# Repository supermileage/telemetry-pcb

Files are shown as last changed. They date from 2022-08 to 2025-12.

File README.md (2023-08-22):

# Telemetry PCB

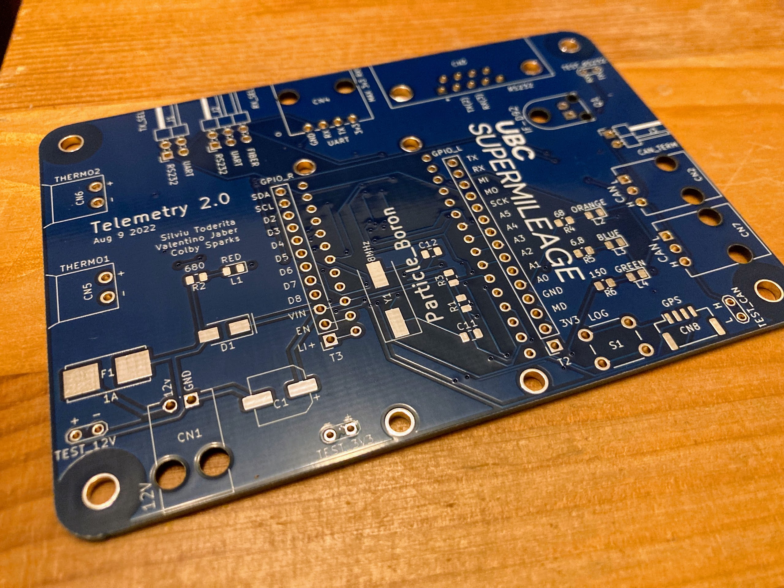
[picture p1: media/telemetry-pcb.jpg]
Telemetry 2.0 Circuit Board


Printed Circuit Board design for the Supermileage Telemetry Module. More information on its functionality can be found in the [firmware repo](https://github.com/supermileage/telemetry-firmware/tree/master).

The PCB is a 2-layer design, intended to be manufactured with 1oz copper. It was designed to be as small and as versatile as possible, to fit into tight spaces on multiple vehicles. The PCB features:

- Particle Boron Microcontroller with built-in LTE Connection
- LMS6DSO Accelerometer & Gyroscope
- 2x MAX31855K Thermocouple ICs with 2 Thermocouple inputs
- MCP2515 CAN Controller, TCAN332 CAN Transciever, 2x CAN ports
- Switchable TTL UART, RS232 UART (MAX3232), or optical UART (IF-D92)
- Connector for external i2c GPS module
- LEDs and button for monitoring & control

## Schematic Preview

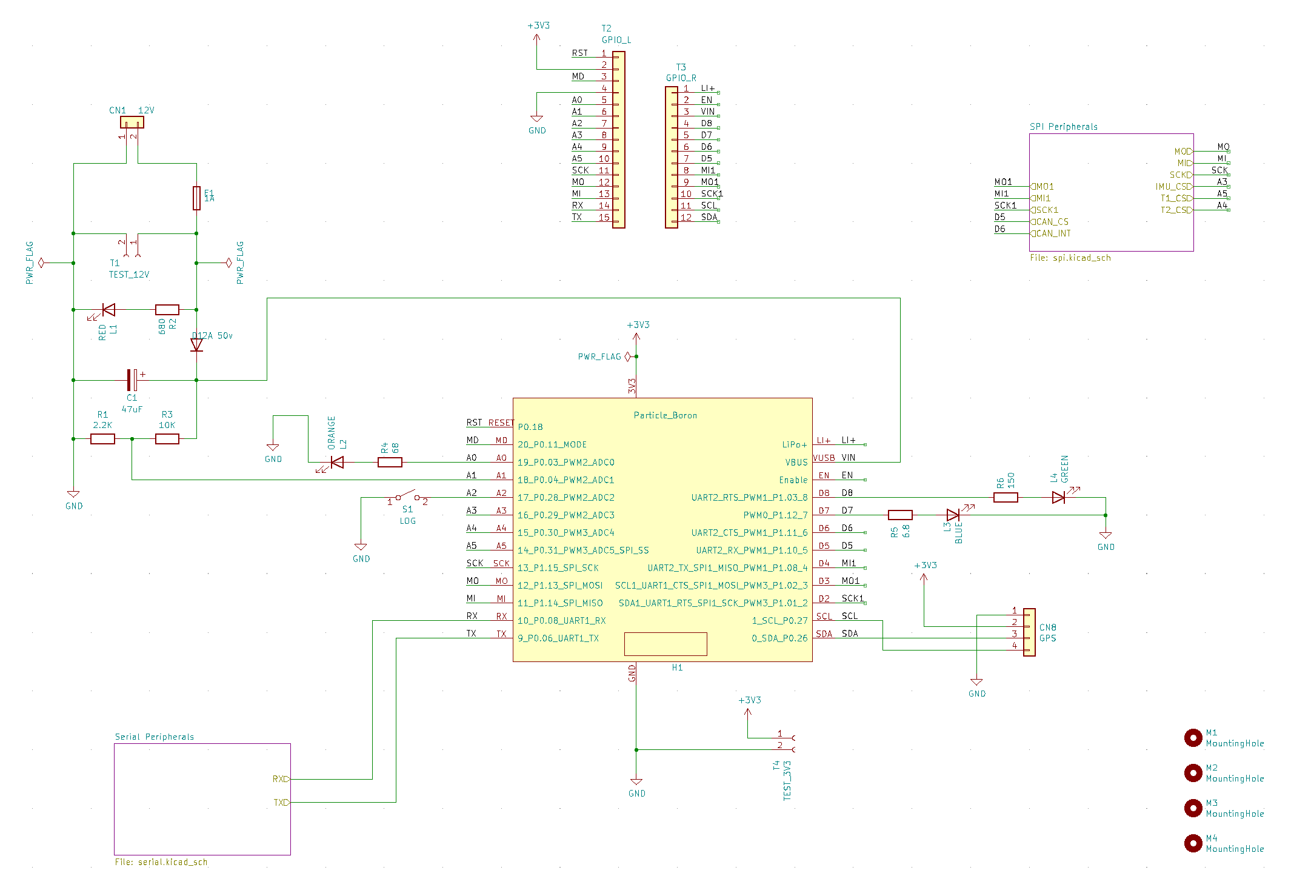
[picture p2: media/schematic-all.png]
Schematic All


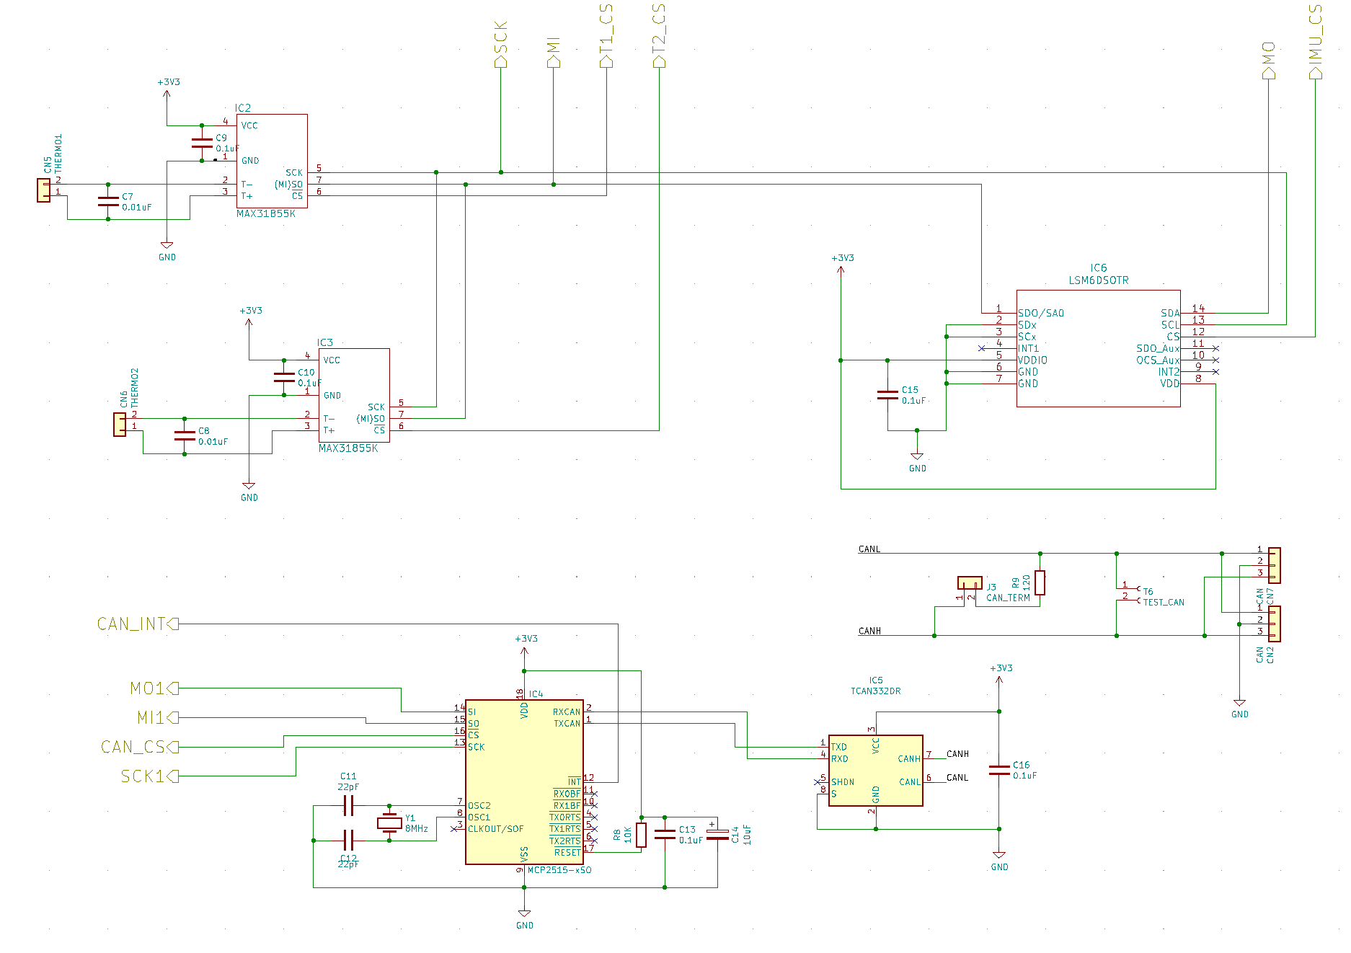
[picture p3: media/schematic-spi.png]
Schematic SPI


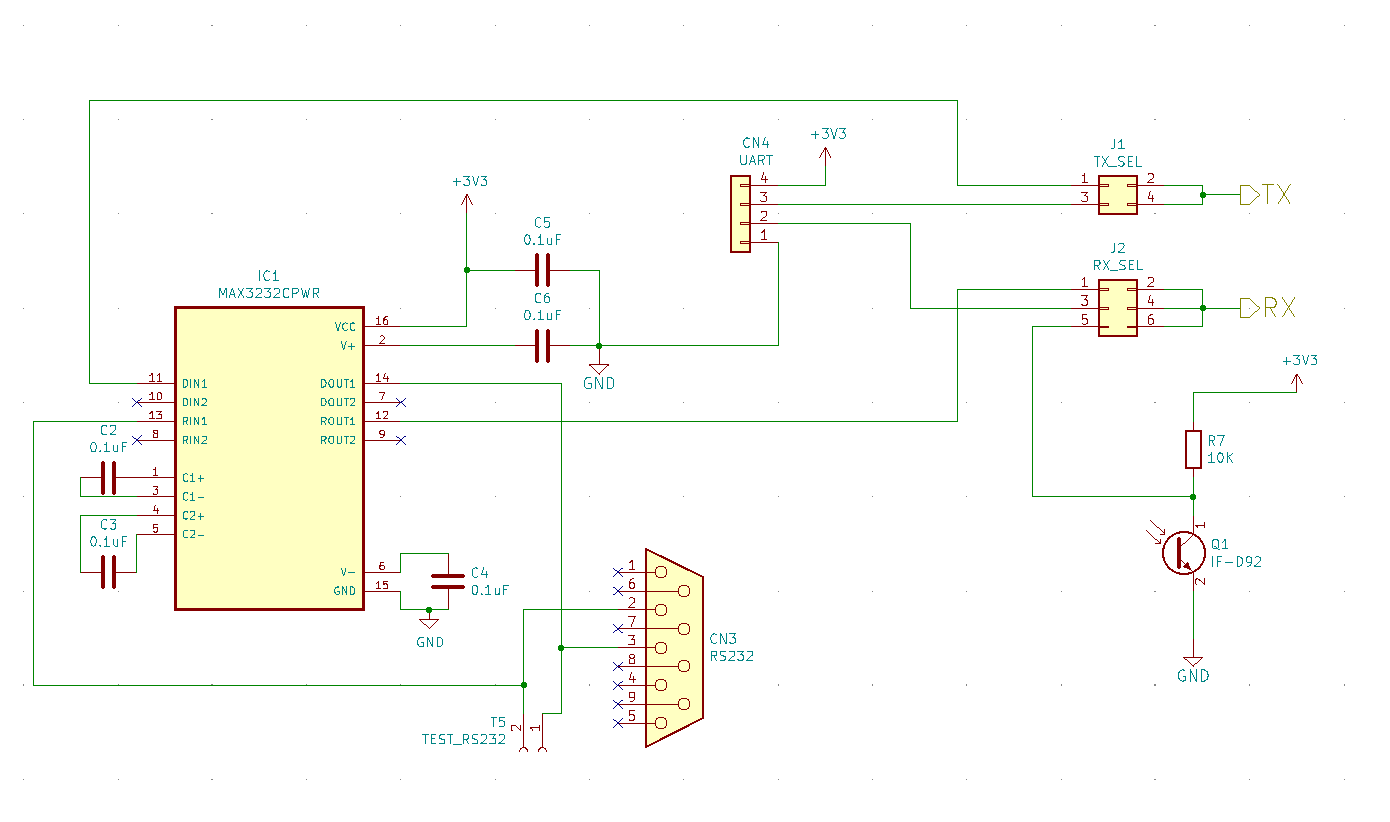
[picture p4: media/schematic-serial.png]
Schematic Serial


## PCB Preview

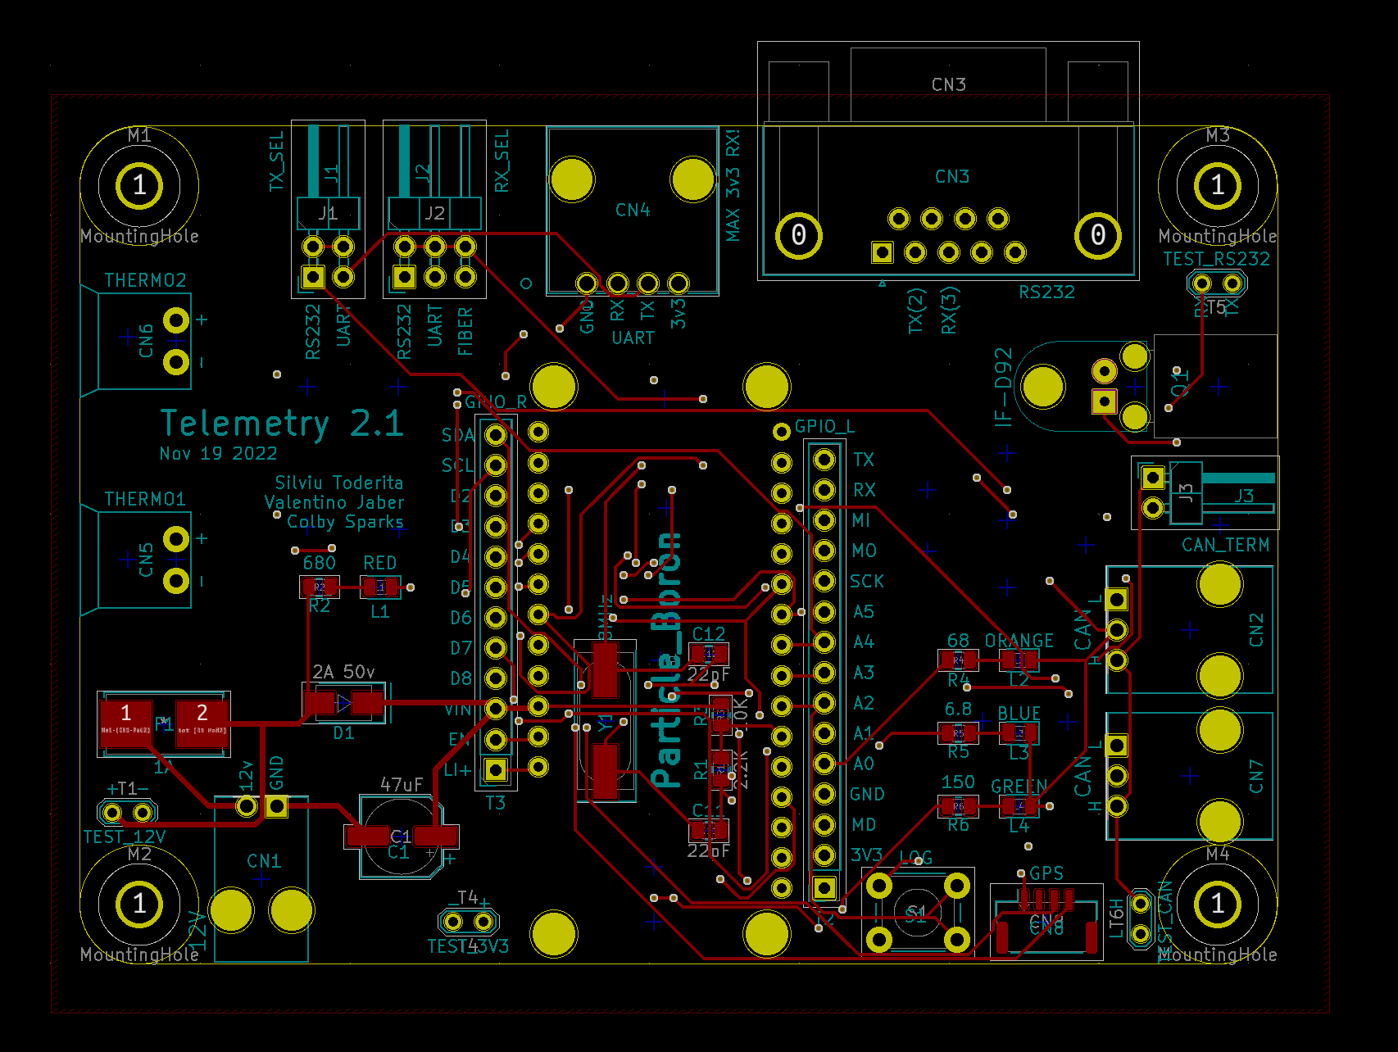
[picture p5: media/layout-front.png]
Layout Front


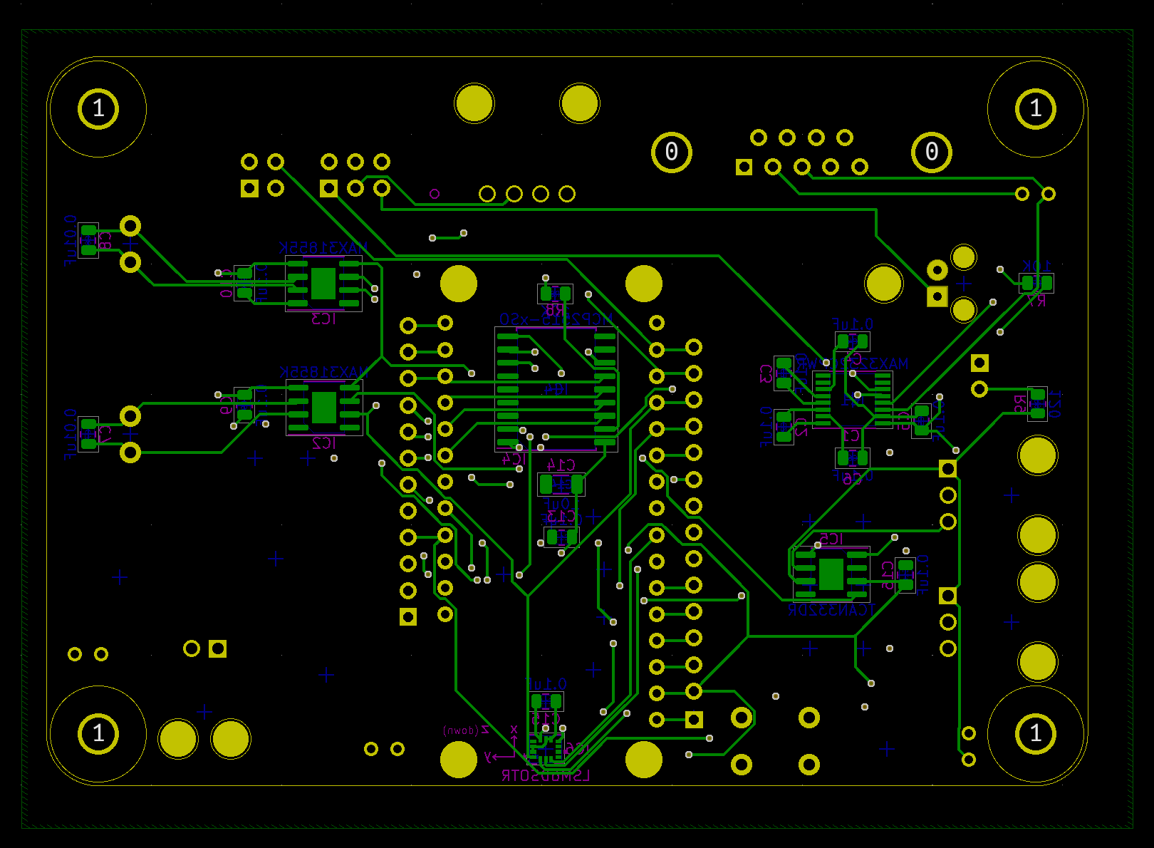
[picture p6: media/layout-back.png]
Layout Back


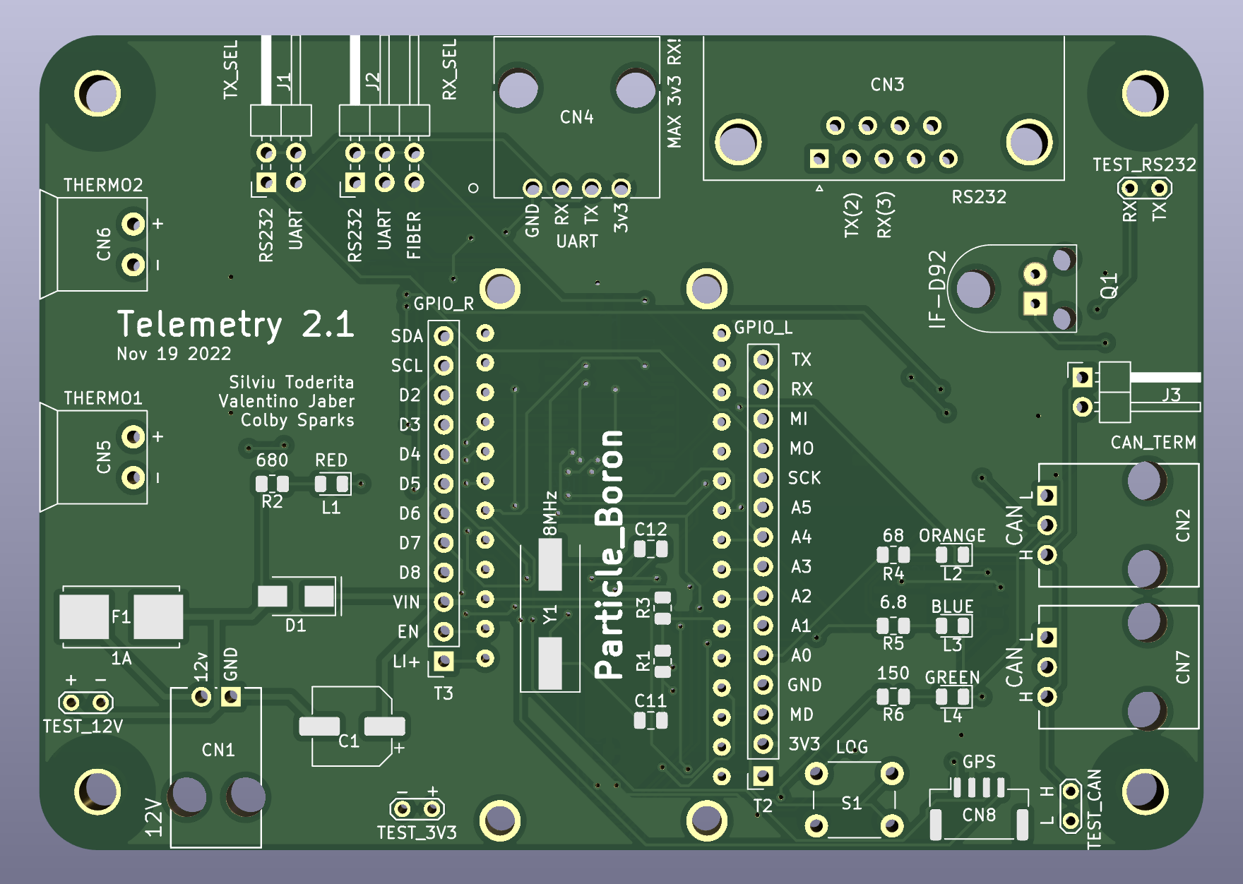
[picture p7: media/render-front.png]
Render Front


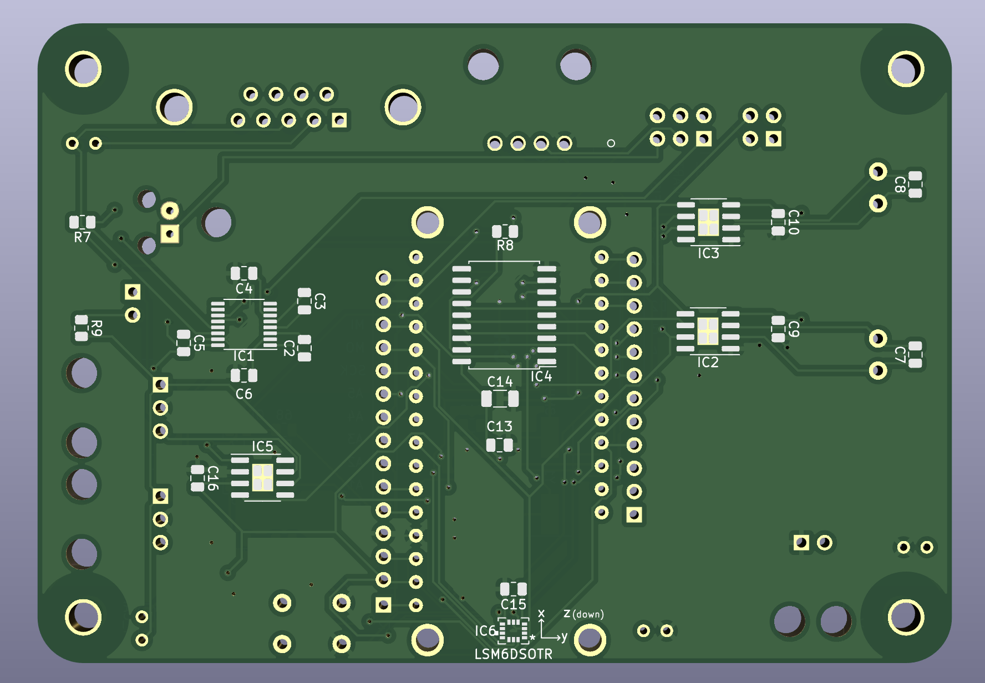
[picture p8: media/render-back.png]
Render Back


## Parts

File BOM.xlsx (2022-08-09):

*Designator | *Qty | Manufacturer | *Mfg Part # | Description / Value | *Package/Footprint | Type | DigiKey URL | Source
C1 | 1 | Wurth Elektronik | 865080543009 | CAP ALUM 47UF 20% 35V SMD | Radial 6.3mm | SMD | https://www.digikey.ca/en/products/detail/w%C3%BCrth-elektronik/865080543009/5728103 | Digikey
C2,C3,C4,C5,C6,C9,C10,C13,C15,C16 | 10 | Samsung Electro-Mechanics | CL21B104KBCNNNC | CAP CER 0.1UF 50V X7R 0805 | 0805 | SMD | https://www.digikey.ca/en/products/detail/samsung-electro-mechanics/CL21B104KBCNNNC/3886661 | Digikey
C7,C8 | 2 | Kemet | C0805C103K1RAC7800 | CAP CER 10000PF 100V X7R 0805 | 0805 | SMD | https://www.digikey.ca/en/products/detail/kemet/C0805C103K1RAC7800/411158 | Digikey
C11,C12 | 2 | Kemet | C0805C220J5GAC7800 | CAP CER 22PF 50V C0G/NP0 0805 | 0805 | SMD | https://www.digikey.ca/en/products/detail/kemet/C0805C220J5GAC7800/411112 | Digikey
C14 | 1 | KYOCERA AVX | TAJA106K016RNJ | CAP TANT 10UF 10% 16V 1206 | 1206 | SMD | https://www.digikey.ca/en/products/detail/kyocera-avx/TAJA106K016RNJ/563762 | Digikey
CN1 | 1 | Molex | 705510001 | CONN HEADER R/A 2POS 2.54MM | 1x4POS | Through-Hole | https://www.digikey.ca/en/products/detail/molex/0705510001/2421652 | Digikey
CN2,CN7 | 2 | Molex | 705510002 | CONN HEADER R/A 3POS 2.54MM | 1x3POS | Through-Hole | https://www.digikey.ca/en/products/detail/molex/0705510002/3468756?s=N4IgTCBcDaIOwAYCsSCMCMQLoF8g | Digikey
CN3 | 1 | Amphenol ICC (FCI) | LD09P13A4GX00LF | CONN D-SUB PLUG 9POS R/A SLDR | D-SUB 9POS | Through-Hole | https://www.digikey.ca/en/products/detail/amphenol-icc-fci/LD09P13A4GX00LF/4997285 | Digikey
CN4 | 1 | Molex | 0705510003 | CONN HEADER R/A 4POS 2.54MM | 1x5POS | Through-Hole | https://www.digikey.ca/en/products/detail/molex/0705510003/3468757 | Digikey
CN5,CN6 | 2 | TE Connectivity AMP Connectors | 284512-2 | TERM BLOCK HDR 2POS 90DEG 3.5MM | 1x2POS | Through-Hole | https://www.digikey.ca/en/products/detail/te-connectivity/284512-2/1150185 | Digikey
CN8 | 1 | JST Sales America Inc. | S4B-ZR-SM4A-TF(LF)(SN) | CONN HEADER SMD R/A 4POS 1.5MM | 1x4POS | SMD | https://www.digikey.ca/en/products/detail/jst-sales-america-inc/S4B-ZR-SM4A-TF-LF-SN/926602 | Digikey
D1 | 1 | Diodes Incorporated | S1A-13-F | DIODE GEN PURP 50V 1A SMA | SMA | SMD | https://www.digikey.ca/en/products/detail/diodes-incorporated/S1A-13-F/749977 | Digikey
F1 | 1 | Littelfuse Inc. | 0154001.DRL | FUSE BRD MNT 1A 125VAC/VDC 2SMD | 2-SMD | SMD | https://www.digikey.ca/en/products/detail/littelfuse-inc/0154001-DRL/2520371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 | Digikey
H1 (A) | 1 | Sullins Connector Solutions | S7014-ND | CONN HDR 16POS 0.1 TIN PCB | 1x16POS | Through-Hole | https://www.digikey.ca/en/products/detail/sullins-connector-solutions/PPTC161LFBN-RC/810154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 | Digikey
H1 (B) | 1 | Sullins Connector Solutions | S6100-ND | CONN HDR 12POS 0.1 TIN PCB | 1x12POS | Through-Hole | https://www.digikey.ca/en/products/detail/sullins-connector-solutions/PPTC121LFBN-RC/807231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 | Digikey
IC1 | 1 | Analog Devices Inc./Maxim Integrated | MAX3232ECUE+T | IC TRANSCEIVER FULL 2/2 16TSSOP | 16-TSSOP | SMD | https://www.digikey.ca/en/products/detail/analog-devices-inc-maxim-integrated/MAX3232ECUE-T/1515210 | Digikey
IC2,IC3 | 2 | Maxim Integrated | MAX31855KASA+T | IC CONV THERMOCOUPLE-DGTL SOIC | 8-SOIC | SMD | https://www.digikey.ca/en/products/detail/analog-devices-inc-maxim-integrated/MAX31855KASA/2591564 | Digikey
IC4 | 1 | Microchip Technology | MCP2515T-I/SOCT-ND | IC CAN CONTROLLER W/SPI 18SOIC | 18-SOIC | SMD | https://www.digikey.ca/en/products/detail/microchip-technology/MCP2515T-I-SO/593681 | ???
IC5 | 1 | Analog Devices Inc./Maxim Integrated | MAX33041EASA+ | IC CAN TXRX 3.3V 2MBPS SOIC | 8-SOIC | SMD | https://www.digikey.ca/en/products/detail/analog-devices-inc-maxim-integrated/MAX33041EASA/15286828 | Digikey
IC6 | 1 | STMicroelectronics | LSM6DSOTR | CONSUMER MEMS | 14-LGA | SMD | https://www.digikey.ca/en/products/detail/stmicroelectronics/LSM6DSOTR/9586579 | Digikey
J1 | 1 | Amphenol ICC (FCI) | 10129382-906003BLF | CONN HEADER R/A 6POS 2.54MM | 2x3POS | Through-Hole | https://www.digikey.ca/en/products/detail/amphenol-icc-fci/10129382-906003BLF/7916129 | Digikey
J2 | 1 | Sullins Connector Solutions | PRPC002DBAN-M71RC | CONN HEADER R/A 4POS 2.54MM | 2x2POS | Through-Hole | https://www.digikey.ca/en/products/detail/sullins-connector-solutions/PRPC002DBAN-M71RC/2775721 | Digikey
J3 | 1 | Amphenol ICC (FCI) | 10129379-902001BLF | CONN HEADER R/A 2POS 2.54MM | 1x2POS | Through-Hole | https://www.digikey.ca/en/products/detail/amphenol-icc-fci/10129379-902001BLF/7915977 | Digikey
L1 | 1 | Lite-On Inc. | LTST-C170KRKT | LED RED CLEAR SMD (680) | 0805 | SMD | https://www.digikey.ca/en/products/detail/lite-on-inc/LTST-C170KRKT/386779 | Digikey
L2 | 1 | Lite-On Inc. | LTST-C170KFKT | LED ORANGE CLEAR SMD (68) | 0805 | SMD | https://www.digikey.ca/en/products/detail/lite-on-inc/LTST-C170KFKT/386775 | Digikey
L3 | 1 | Lite-On Inc. | LTST-C170TBKT | LED BLUE CLEAR SMD (6.8) | 0805 | SMD | https://www.digikey.ca/en/products/detail/lite-on-inc/LTST-C170TBKT/388527 | Digikey
L4 | 1 | Lite-On Inc. | LTST-C170GKT | LED GREEN CLEAR SMD (150) | 0805 | SMD | https://www.digikey.ca/en/products/detail/lite-on-inc/LTST-C170GKT/269226 | Digikey
Q1 | 1 | Industrial Fiber Optics | IF-D92 | PHOTOTRANSISTOR FIBER OPTIC |  | Through-Hole | https://www.digikey.ca/en/products/detail/industrial-fiber-optics/IF-D92/243778?s=N4IgTCBcDaIJYDMC0ATAnBAugXyA | Digikey
R1 | 1 | Stackpole Electronics Inc | RMCF0805FT2K20 | RES 2.2K OHM 1% 1/8W 0805 | 0805 | SMD | https://www.digikey.ca/en/products/detail/stackpole-electronics-inc/RMCF0805FT2K20/1760345 | Digikey
R2 | 1 | Stackpole Electronics Inc | RMCF0805FT680R | RES 680 OHM 1% 1/8W 0805 | 0805 | SMD | https://www.digikey.ca/en/products/detail/stackpole-electronics-inc/RMCF0805FT680R/1760531 | Digikey
R3,R7,R8 | 3 | Stackpole Electronics Inc | RMCF0805JT10K0 | RES 10K OHM 5% 1/8W 0805 | 0805 | SMD | https://www.digikey.ca/en/products/detail/stackpole-electronics-inc/RMCF0805JT10K0/1757762 | Digikey
R4 | 1 | Stackpole Electronics Inc | RMCF0805FT68R0 | RES 68 OHM 1% 1/8W 0805 | 0805 | SMD | https://www.digikey.ca/en/products/detail/stackpole-electronics-inc/RMCF0805FT68R0/1713312 | Digikey
R5 | 1 | YAGEO | RC0805FR-076R8L | RES 6.8 OHM 1% 1/8W 0805 | 0805 | SMD | https://www.digikey.ca/en/products/detail/yageo/RC0805FR-076R8L/728065 | Digikey
R6 | 1 | Stackpole Electronics Inc | RMCF0805JT150R | RES 150 OHM 5% 1/8W 0805 | 0805 | SMD | https://www.digikey.ca/en/products/detail/stackpole-electronics-inc/RMCF0805JT150R/1757820 | Digikey
R9 | 1 | Stackpole Electronics Inc | RMCF0805JT120R | RES 120 OHM 5% 1/8W 0805 | 0805 | SMD | https://www.digikey.ca/en/products/detail/stackpole-electronics-inc/RMCF0805JT120R/1757777 | Digikey
S1 | 1 | TE Connectivity ALCOSWITCH Switches | 3-1825910-1 | SWITCH TACTILE SPST-NO 0.05A 24V | 6mm | Through-Hole | https://www.digikey.ca/en/products/detail/te-connectivity-alcoswitch-switches/3-1825910-1/1632529 | Digikey
Y1 | 1 | Abracon LLC | ABLS2-8.000MHZ-D4Y-T | 8 MHz ±30ppm Crystal 18pF 80 Ohms HC-49/US | HC-49/US | SMD | https://www.digikey.ca/en/products/detail/abracon-llc/ABLS2-8-000MHZ-D4Y-T/2001231 | Digikey
Not on PCB:
Microcontroller | 1 | Particle Industries, Inc. | BRN402 | BORON LTE |  | Through-Hole | https://www.digikey.ca/en/products/detail/particle-industries-inc/BRN402/9681356 | ???
GPS | 1 | SparkFun Electronics | GPS-15210 | SPARKFUN GPS BREAKOUT - CHIP ANT |  |  | https://www.digikey.ca/en/products/detail/sparkfun-electronics/GPS-15210/10064422 | Digikey
Mounting Screws | 4 |  |  | M3x6 Screw |  |  |  | Lee's Electronics
Jumpers | 3 | Sullins Connector Solutions | QPC02SXGN-RC | CONN JUMPER SHORTING .100" GOLD | 1x2POS |  | https://www.digikey.ca/en/products/detail/sullins-connector-solutions/QPC02SXGN-RC/2618262 | Digikey
Connector Power | 1 | Molex | 0050579702 | CONN FEMALE HSG POS LTCH 2CKT | 1x2POS |  | https://www.digikey.ca/en/products/detail/molex/0050579702/2421209 | Digikey
Connector CAN | 2 | Molex | 50579703 | CONN HSG 3POS .100 SINGLE VER N | 1x3POS |  | https://www.digikey.ca/en/products/detail/molex/0050579703/2731437 | Digikey
Connector UART | 1 | Molex | 0050579704 | CONN HSG 4POS .100 SINGLE VER N | 1x4POS |  | https://www.digikey.ca/en/products/detail/molex/0050579704/2731443 | Digikey
Connector Thermocouple | 2 | TE Connectivity AMP Connectors | 284506-2 | TERM BLOCK PLUG 2POS STR 3.5MM | 1x2POS |  | https://www.digikey.ca/en/products/detail/te-connectivity-amp-connectors/284506-2/1827035 | Digikey
Molex Pins | 12 | Molex | 16020086 | CONN SOCKET 22-24AWG CRIMP TIN |  |  | https://www.digikey.ca/en/products/detail/molex/0016020086/467788 | Digikey
Connector GPS | 1 | JST Sales America Inc. | ZHR-4 | CONN RCPT HSG 4POS 1.50MM | 1x4POS |  | https://www.digikey.ca/en/products/detail/jst-sales-america-inc/ZHR-4/608643 | ???
GPS Pre-Crimped Pins | 1 | JST Sales America Inc. | ASZHSZH28K51 | JUMPER SZH-002T-P0.5 X2 2" |  |  | https://www.digikey.ca/en/products/detail/jst-sales-america-inc/ASZHSZH28K51/6009454 | Digikey
Spare Fuse |  | Bel Fuse Inc. | 0679L1000-05 | FUSE BRD MNT 1A 125VAC/VDC | 2-SMD |  | https://www.digikey.ca/en/products/detail/bel-fuse-inc/0679L1000-05/5844030 | Digikey
ECU Cable |  |  |  | RS232 Cable (Straight-Through) |  |  |  | Amazon
FC Fiber |  |  |  | 2.2mm Fiber Optic Wire
Thermocouples |  |  |  | 1M insulated K-Type Thermocouple
Case |  |  |  | 3D Printed Custom Case
USB Cable |  |  |  | Micro-USB Cable
 |  |  |  |  |  | u

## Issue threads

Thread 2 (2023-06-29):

Fix button footprint

cosparks, 2023-06-29:
Orientaion of connectors is wrong.  Swap 3.3V and ground

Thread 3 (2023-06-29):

Add through-hole connector with latch for GPS

cosparks, 2023-06-29:
The surface mount connector for GPS has been problematic.  There is no latch so it can be pulled out very easily, and twice we have stripped the pads by pushing too hard against it.  We ran into both of these issues during competition.

See if a molex micro or nanofit connector would fit on the board.

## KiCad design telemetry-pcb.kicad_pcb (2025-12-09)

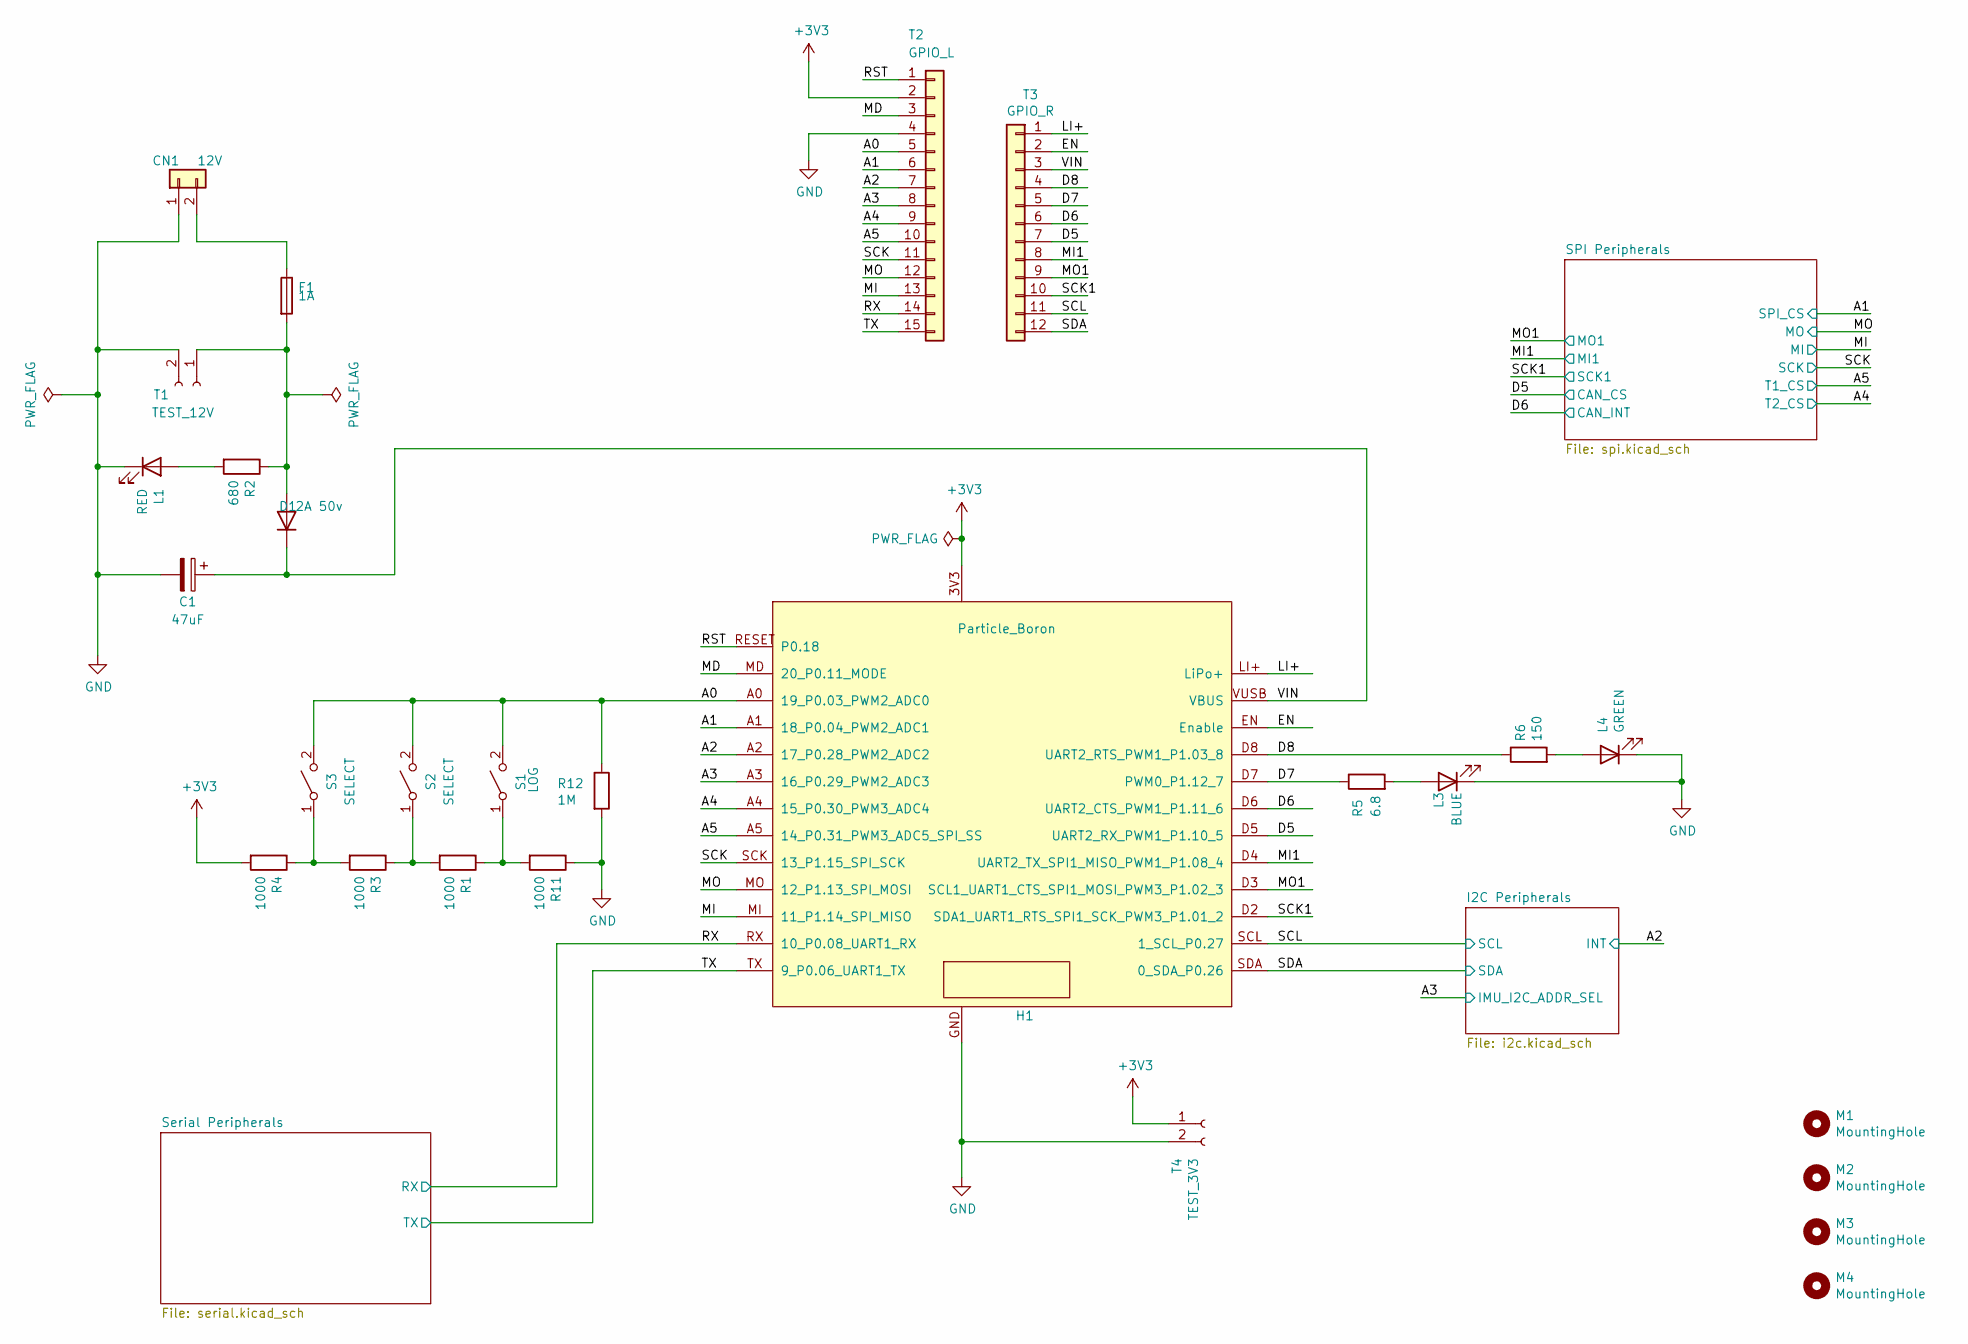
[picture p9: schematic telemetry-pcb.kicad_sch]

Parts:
C1: 47uF; CP_Elec_6.3x5.4
CN1: 12V; molex_sl_1x02_horizontal
D1: 2A 50v; D_SMA
F1: 1A; 0154001.DRL
H1: Particle_Boron; Particle_boron
L1: RED; LED_0805_2012Metric
L3: BLUE; LED_0805_2012Metric
L4: GREEN; LED_0805_2012Metric
M1, M2, M3, M4: MountingHole; MountingHole_3.2mm_M3
R1, R3, R4, R11: 1000; R_0805_2012Metric
R2: 680; R_0805_2012Metric
R5: 6.8; R_0805_2012Metric
R6: 150; R_0805_2012Metric
R12: 1M; R_0805_2012Metric
S1: LOG; SW_PUSH_6mm_H13mm
S2, S3: SELECT; SW_PUSH_6mm_H13mm
T1: TEST_12V; TestPoint_2Pads_Pitch2.54mm_Drill0.8mm
T2: GPIO_L; Boron_Pins_L
T3: GPIO_R; Boron_Pins_R
T4: TEST_3V3; TestPoint_2Pads_Pitch2.54mm_Drill0.8mm

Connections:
+3V3: H1.3V3, R4.2, T2.2, T4.1; also elsewhere on the board
/A0: H1.A0 (19_P0.03_PWM2_ADC0), R12.1, S1.2 (B), S2.2 (B), S3.2 (B), T2.5
/A1: H1.A1 (18_P0.04_PWM2_ADC1), T2.6; also elsewhere on the board
/A2: H1.A2 (17_P0.28_PWM2_ADC2), T2.7; also elsewhere on the board
/A3: H1.A3 (16_P0.29_PWM2_ADC3), T2.8; also elsewhere on the board
/A4: H1.A4 (15_P0.30_PWM3_ADC4), T2.9; also elsewhere on the board
/A5: H1.A5 (14_P0.31_PWM3_ADC5_SPI_SS), T2.10; also elsewhere on the board
/D5: H1.D5 (UART2_RX_PWM1_P1.10_5), T3.7; also elsewhere on the board
/D6: H1.D6 (UART2_CTS_PWM1_P1.11_6), T3.6; also elsewhere on the board
/D7: H1.D7 (PWM0_P1.12_7), R5.1, T3.5
/D8: H1.D8 (UART2_RTS_PWM1_P1.03_8), R6.1, T3.4
/EN: H1.EN (Enable), T3.2
/LI+: H1.LI+ (LiPo+), T3.1
/MD: H1.MD (20_P0.11_MODE), T2.3
/MI: H1.MI (11_P1.14_SPI_MISO), T2.13; also elsewhere on the board
/MI1: H1.D4 (UART2_TX_SPI1_MISO_PWM1_P1.08_4), T3.8; also elsewhere on the board
/MO: H1.MO (12_P1.13_SPI_MOSI), T2.12; also elsewhere on the board
/MO1: H1.D3 (SCL1_UART1_CTS_SPI1_MOSI_PWM3_P1.02_3), T3.9; also elsewhere on the board
/RST: H1.RESET (P0.18), T2.1
/RX: H1.RX (10_P0.08_UART1_RX), T2.14; also elsewhere on the board
/SCK: H1.SCK (13_P1.15_SPI_SCK), T2.11; also elsewhere on the board
/SCK1: H1.D2 (SDA1_UART1_RTS_SPI1_SCK_PWM3_P1.01_2), T3.10; also elsewhere on the board
/SCL: H1.SCL (1_SCL_P0.27), T3.11; also elsewhere on the board
/SDA: H1.SDA (0_SDA_P0.26), T3.12; also elsewhere on the board
/TX: H1.TX (9_P0.06_UART1_TX), T2.15; also elsewhere on the board
/VIN: C1.1, D1.1 (K), H1.VUSB (VBUS), T3.3
GND: C1.2, CN1.1, H1.GND, L1.1 (K), L3.1 (K), L4.1 (K), R11.1, R12.2, T1.2, T2.4, T4.2; also elsewhere on the board
unnamed: CN1.2, F1.1
unnamed: D1.2 (A), F1.2, R2.1, T1.1
unnamed: L1.2 (A), R2.2
unnamed: L3.2 (A), R5.2
unnamed: L4.2 (A), R6.2
unnamed: R1.1, R11.2, S1.1 (A)
unnamed: R1.2, R3.1, S2.1 (A)
unnamed: R3.2, R4.1, S3.1 (A)

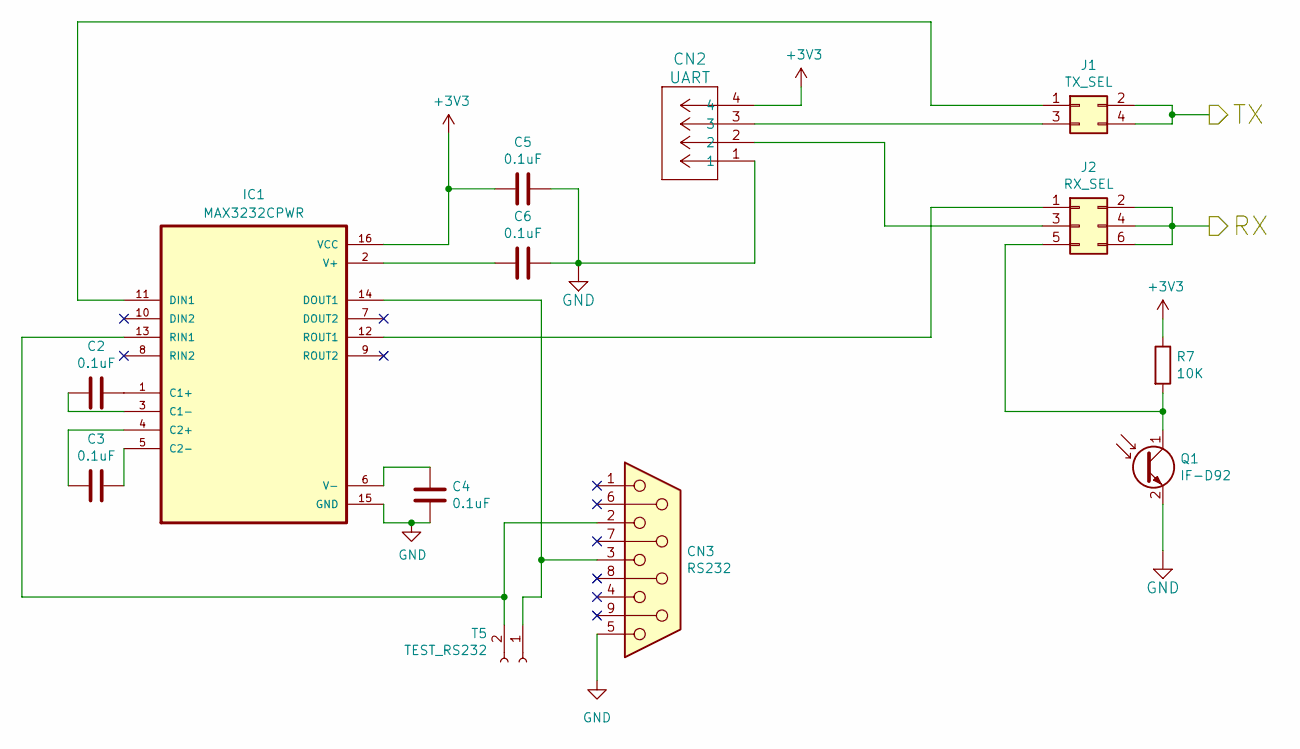
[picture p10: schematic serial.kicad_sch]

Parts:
C2, C3, C4, C5, C6: 0.1uF; C_0805_2012Metric
CN2: UART; CONN_SD-43650-001_04_MOL
CN3: RS232; DSUB-9_Female_Horizontal_P2.77x2.84mm_EdgePinOffset7.70mm_H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
IC1: MAX3232CPWR; TSSOP-16_4.4x5mm_P0.65mm
J1: TX_SEL; PinHeader_2x02_P2.54mm_Horizontal
J2: RX_SEL; PinHeader_2x03_P2.54mm_Horizontal
Q1: IF-D92
R7: 10K; R_0805_2012Metric
T5: TEST_RS232; TestPoint_2Pads_Pitch2.54mm_Drill0.8mm

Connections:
+3V3: C5.2, CN2.4, IC1.16 (VCC), R7.1; also elsewhere on the board
/RX: J2.2, J2.4, J2.6; also elsewhere on the board
/TX: J1.2, J1.4; also elsewhere on the board
GND: C4.2, C5.1, C6.1, CN2.1, CN3.5, IC1.15 (GND), Q1.2 (E); also elsewhere on the board
unnamed: C2.1, IC1.1 (C1+)
unnamed: C2.2, IC1.3 (C1-)
unnamed: C3.2, IC1.4 (C2+)
unnamed: C3.1, IC1.5 (C2-)
unnamed: IC1.11 (DIN1), J1.1
unnamed: CN3.3, IC1.14 (DOUT1), T5.1
unnamed: CN3.2, IC1.13 (RIN1), T5.2
unnamed: IC1.12 (ROUT1), J2.1
unnamed: C6.2, IC1.2 (V+)
unnamed: C4.1, IC1.6 (V-)
unnamed: CN2.3, J1.3
unnamed: CN2.2, J2.3
unnamed: J2.5, Q1.1 (C), R7.2

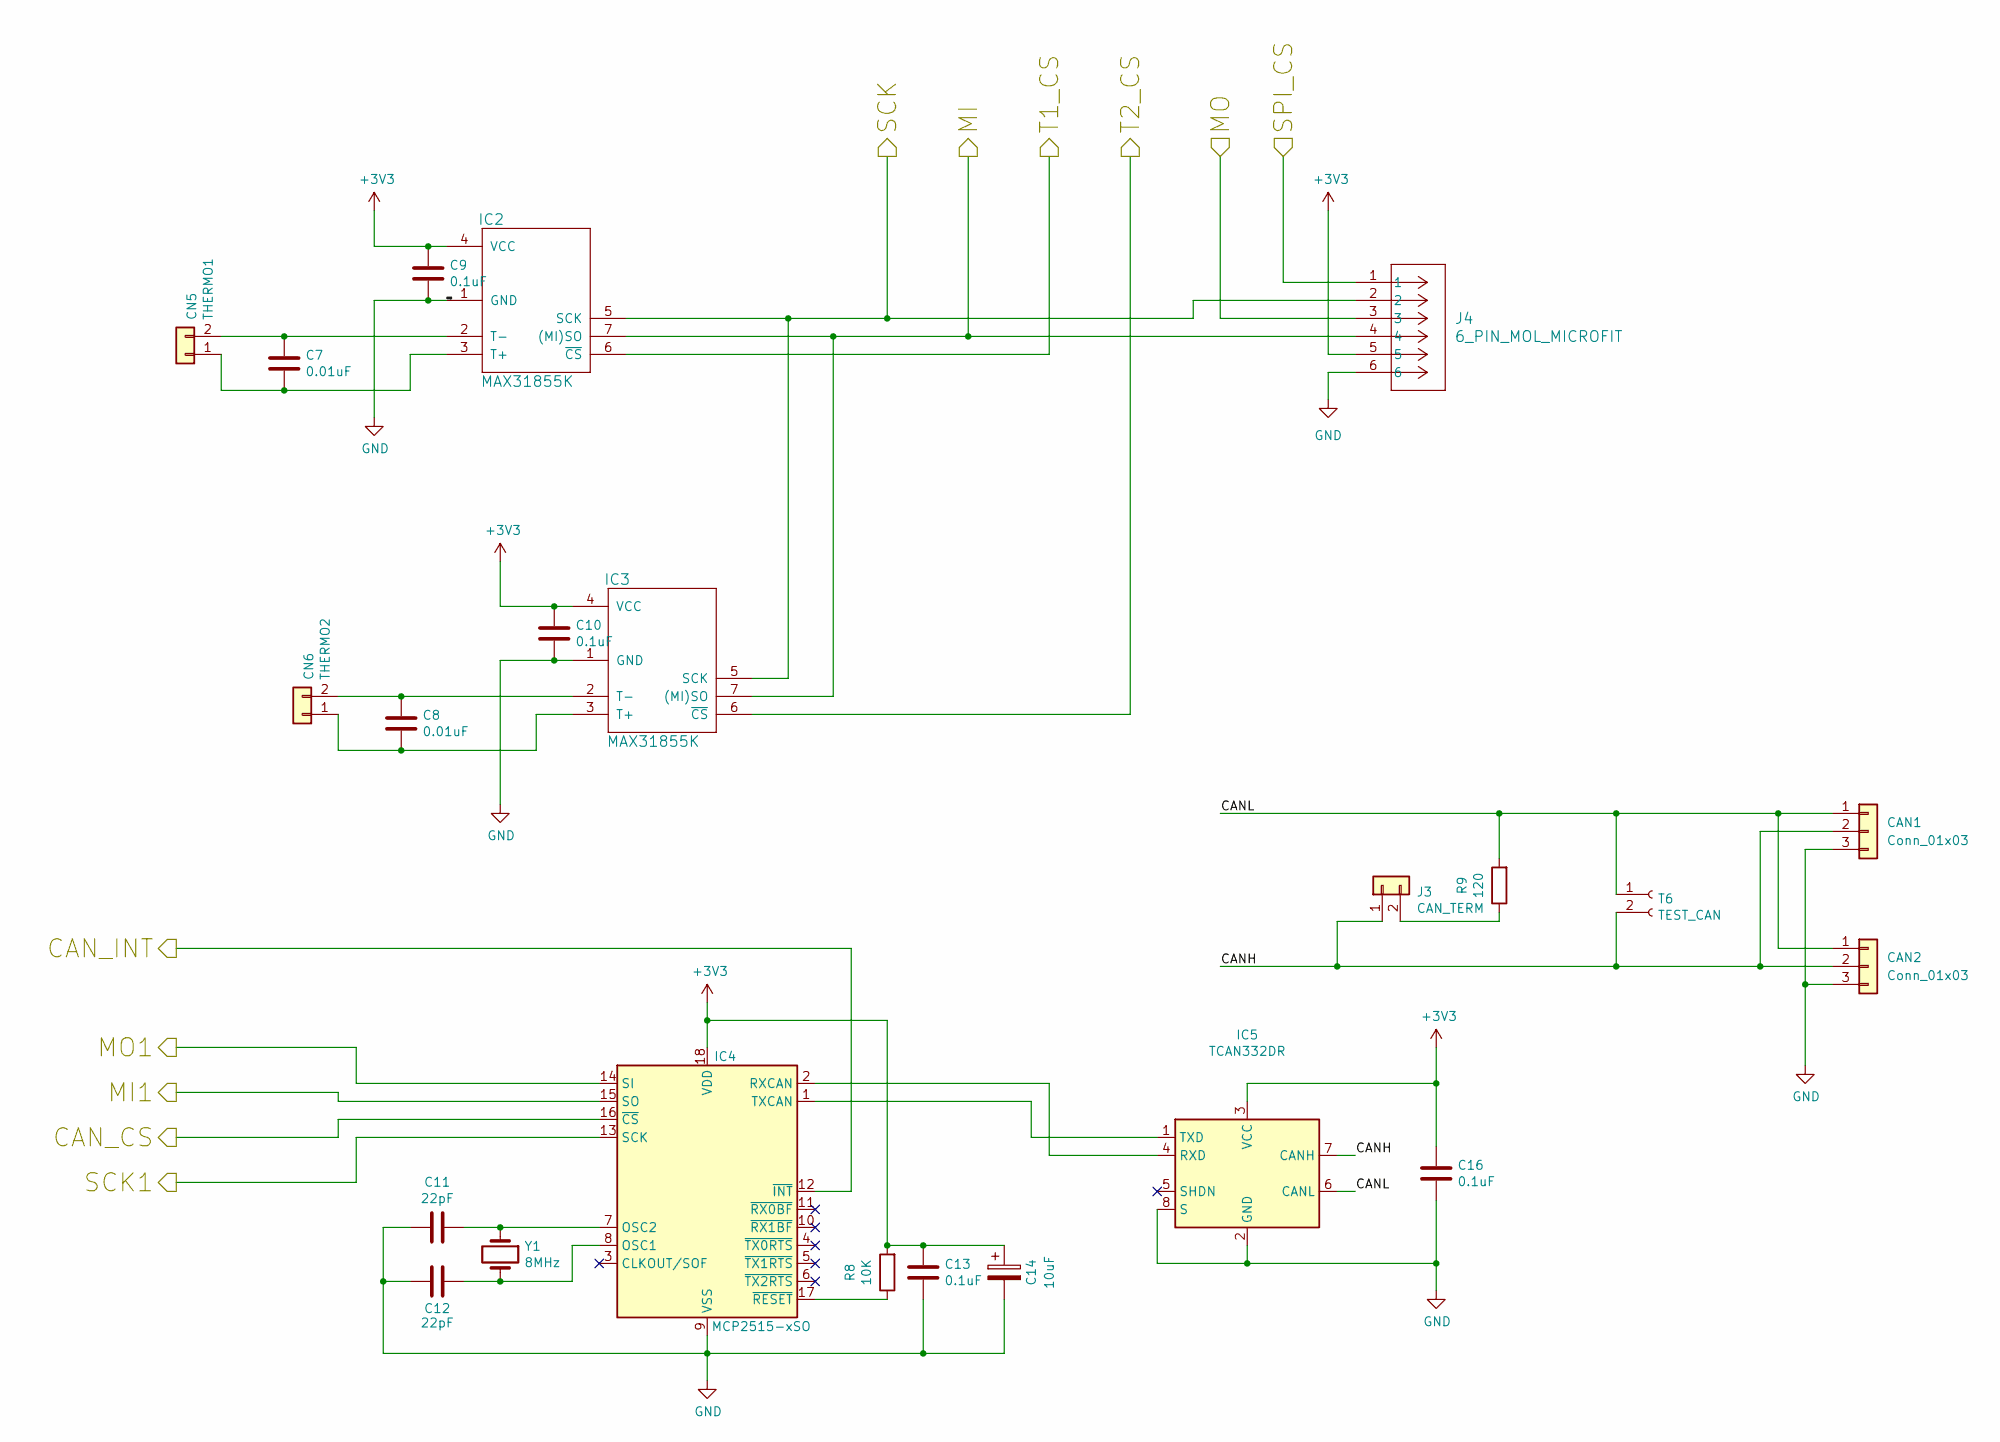
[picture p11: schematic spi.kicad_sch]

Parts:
C7, C8: 0.01uF; C_0805_2012Metric
C9, C10, C13, C16: 0.1uF; C_0805_2012Metric
C11, C12: 22pF; C_0805_2012Metric
C14: 10uF; C_1206_3216Metric
CAN1, CAN2: Conn_01x03; CONN_SD-43650-001_03_MOL
CN5: THERMO1; ScrewTermPlug1x02
CN6: THERMO2; ScrewTermPlug1x02
IC2, IC3: MAX31855K; SOIC-8-1EP_3.9x4.9mm_P1.27mm_EP2.29x3mm
IC4: MCP2515-xSO; SOIC-18W_7.5x11.6mm_P1.27mm
IC5: TCAN332DR; SOIC-8-1EP_3.9x4.9mm_P1.27mm_EP2.29x3mm
J3: CAN_TERM; PinHeader_1x02_P2.54mm_Horizontal
J4: 6_PIN_MOL_MICROFIT; CONN_SD-43045-001_06_MOL
R8: 10K; R_0805_2012Metric
R9: 120; R_0805_2012Metric
T6: TEST_CAN; TestPoint_2Pads_Pitch2.54mm_Drill0.8mm
Y1: 8MHz; Crystal_SMD_HC49-SD

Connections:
+3V3: C9.1, C10.1, C13.2, C14.1, C16.2, IC2.4 (VCC), IC3.4 (VCC), IC4.18 (VDD), IC5.3 (VCC), J4.5, R8.2; also elsewhere on the board
/A1: J4.1; also elsewhere on the board
/A4: IC3.6 (~CS); also elsewhere on the board
/A5: IC2.6 (~CS); also elsewhere on the board
/D5: IC4.16 (~CS); also elsewhere on the board
/D6: IC4.12 (~INT); also elsewhere on the board
/MI: IC2.7 ((MI)SO), IC3.7 ((MI)SO), J4.4; also elsewhere on the board
/MI1: IC4.15 (SO); also elsewhere on the board
/MO: J4.3; also elsewhere on the board
/MO1: IC4.14 (SI); also elsewhere on the board
/SCK: IC2.5 (SCK), IC3.5 (SCK), J4.2; also elsewhere on the board
/SCK1: IC4.13 (SCK); also elsewhere on the board
/SPI Peripherals/CANH: CAN1.2, CAN2.2, IC5.7 (CANH), J3.1, T6.2
/SPI Peripherals/CANL: CAN1.1, CAN2.1, IC5.6 (CANL), R9.2, T6.1
GND: C9.2, C10.2, C11.2, C12.2, C13.1, C14.2, C16.1, CAN1.3, CAN2.3, IC2.1 (GND), IC3.1 (GND), IC4.9 (VSS), IC5.2 (GND), IC5.8 (S), J4.6; also elsewhere on the board
unnamed: C7.2, CN5.1, IC2.3 (T+)
unnamed: C7.1, CN5.2, IC2.2 (T-)
unnamed: C8.2, CN6.1, IC3.3 (T+)
unnamed: C8.1, CN6.2, IC3.2 (T-)
unnamed: C12.1, IC4.8 (OSC1), Y1.2
unnamed: C11.1, IC4.7 (OSC2), Y1.1
unnamed: IC4.2 (RXCAN), IC5.4 (RXD)
unnamed: IC4.1 (TXCAN), IC5.1 (TXD)
unnamed: IC4.17 (~RESET), R8.1
unnamed: J3.2, R9.1

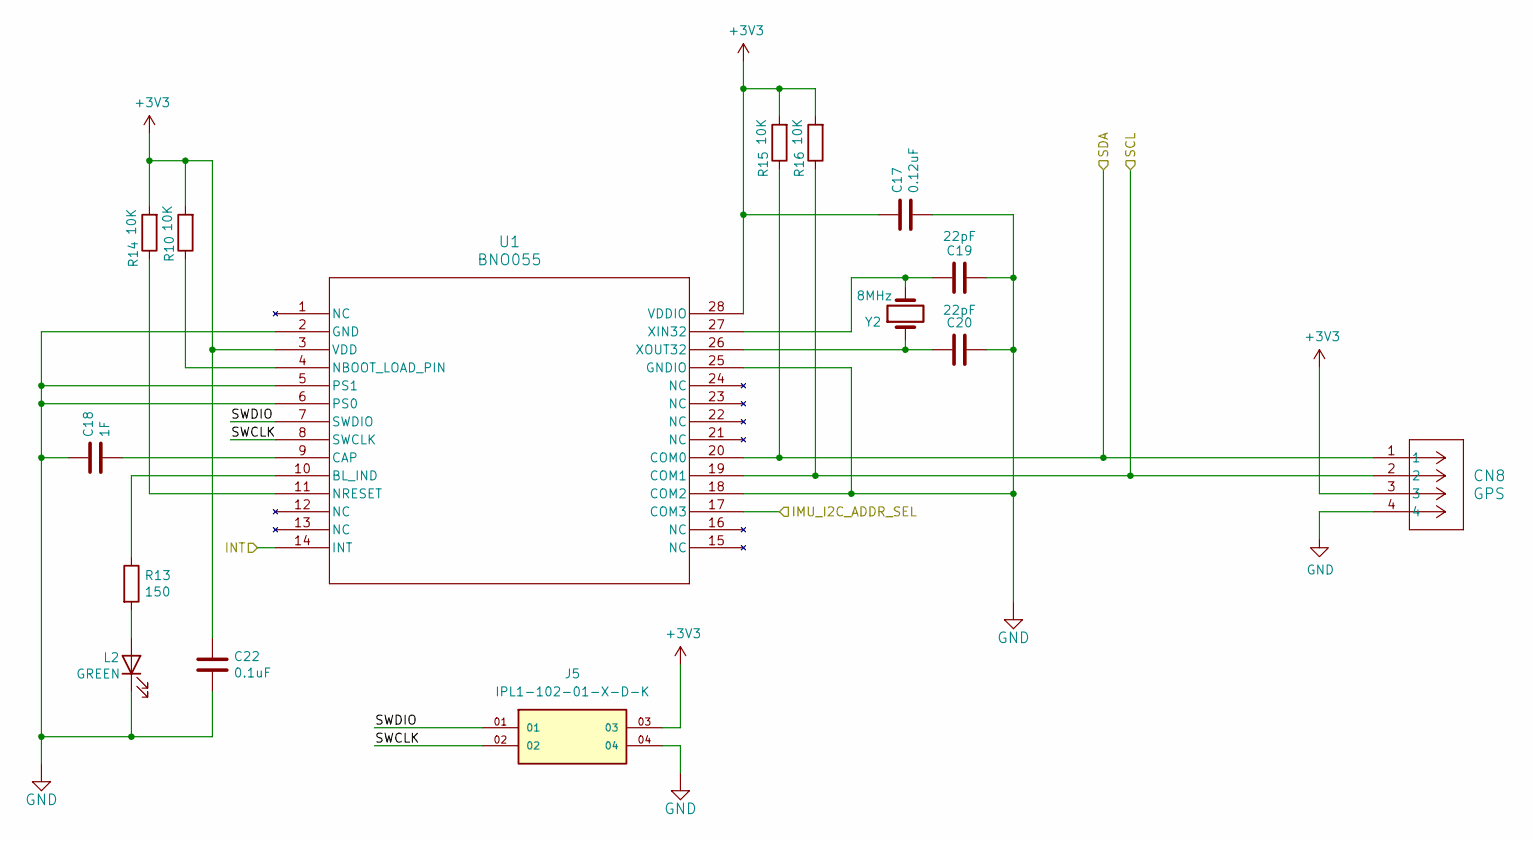
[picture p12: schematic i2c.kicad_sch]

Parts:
C17: 0.12uF; C_0805_2012Metric
C18: 1F; C_1206_3216Metric_Pad1.33x1.80mm_HandSolder
C19, C20: 22pF; C_0805_2012Metric
C22: 0.1uF; C_0805_2012Metric
CN8: GPS; CONN_SD-43650-001_04_MOL
J5: IPL1-102-01-X-D-K; SAMTEC_IPL1-102-01-X-D-K; PARTREV E
L2: GREEN; LED_0805_2012Metric
R10, R14, R15, R16: 10K; R_0805_2012Metric
R13: 150; R_0805_2012Metric
U1: BNO055; QFN_BNO055_BOS
Y2: 8MHz; XTAL_ABS07-32.768KHZ-T

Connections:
+3V3: C17.1, C22.1, CN8.3, J5.03, R10.2, R14.2, R15.2, R16.2, U1.3 (VDD), U1.28 (VDDIO); also elsewhere on the board
/A2: U1.14 (INT); also elsewhere on the board
/A3: U1.17 (COM3); also elsewhere on the board
/I2C Peripherals/SWCLK: J5.02, U1.8 (SWCLK)
/I2C Peripherals/SWDIO: J5.01, U1.7 (SWDIO)
/SCL: CN8.2, R16.1, U1.19 (COM1); also elsewhere on the board
/SDA: CN8.1, R15.1, U1.20 (COM0); also elsewhere on the board
GND: C17.2, C18.1, C19.2, C20.2, C22.2, CN8.4, J5.04, L2.1 (K), U1.2 (GND), U1.5 (PS1), U1.6 (PS0), U1.18 (COM2), U1.25 (GNDIO); also elsewhere on the board
unnamed: L2.2 (A), R13.2
unnamed: R13.1, U1.10 (BL_IND)
unnamed: C18.2, U1.9 (CAP)
unnamed: R10.1, U1.4 (NBOOT_LOAD_PIN)
unnamed: R14.1, U1.11 (NRESET)
unnamed: C19.1, U1.27 (XIN32), Y2.2
unnamed: C20.1, U1.26 (XOUT32), Y2.1

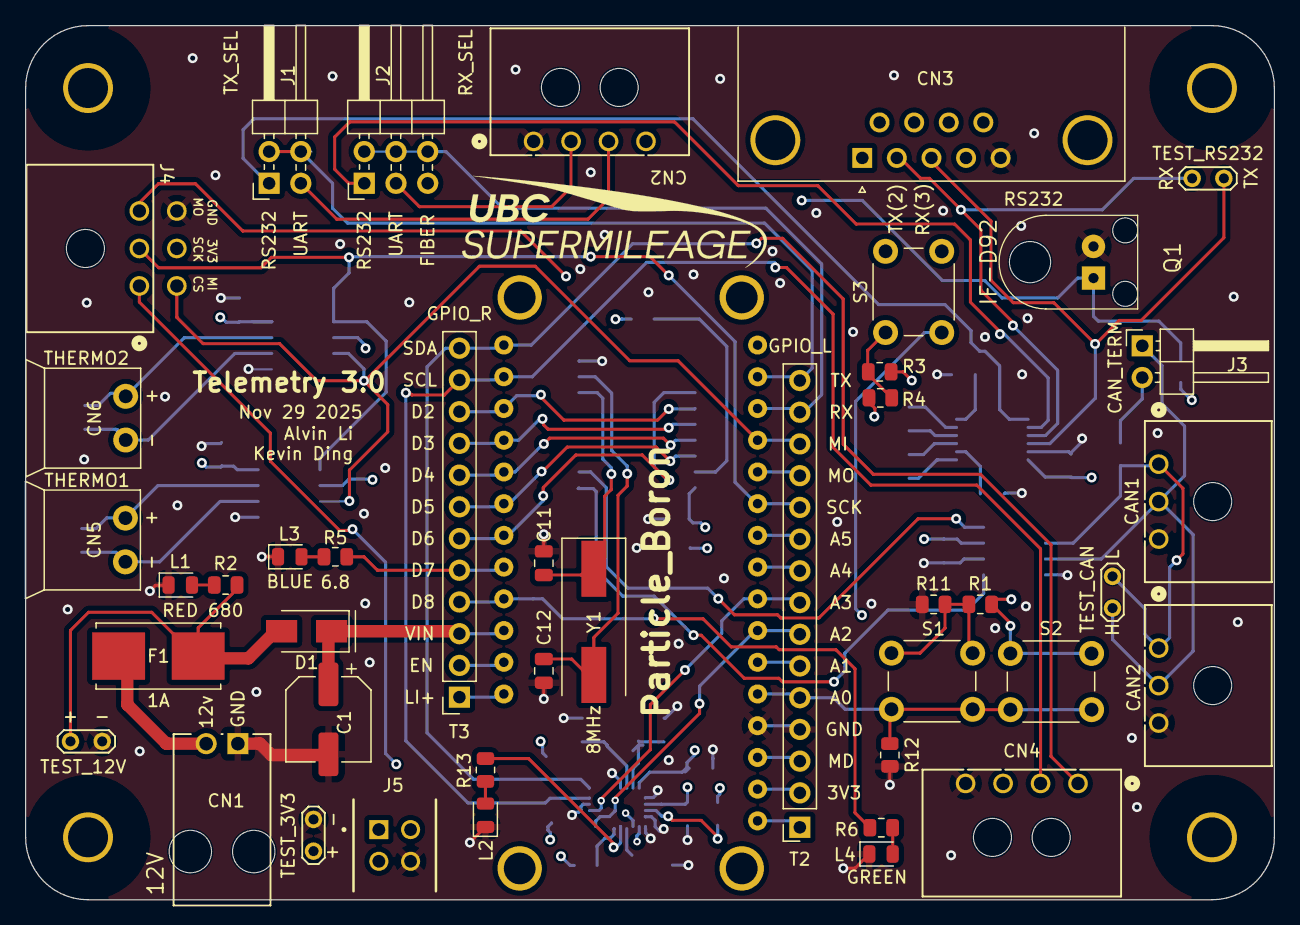
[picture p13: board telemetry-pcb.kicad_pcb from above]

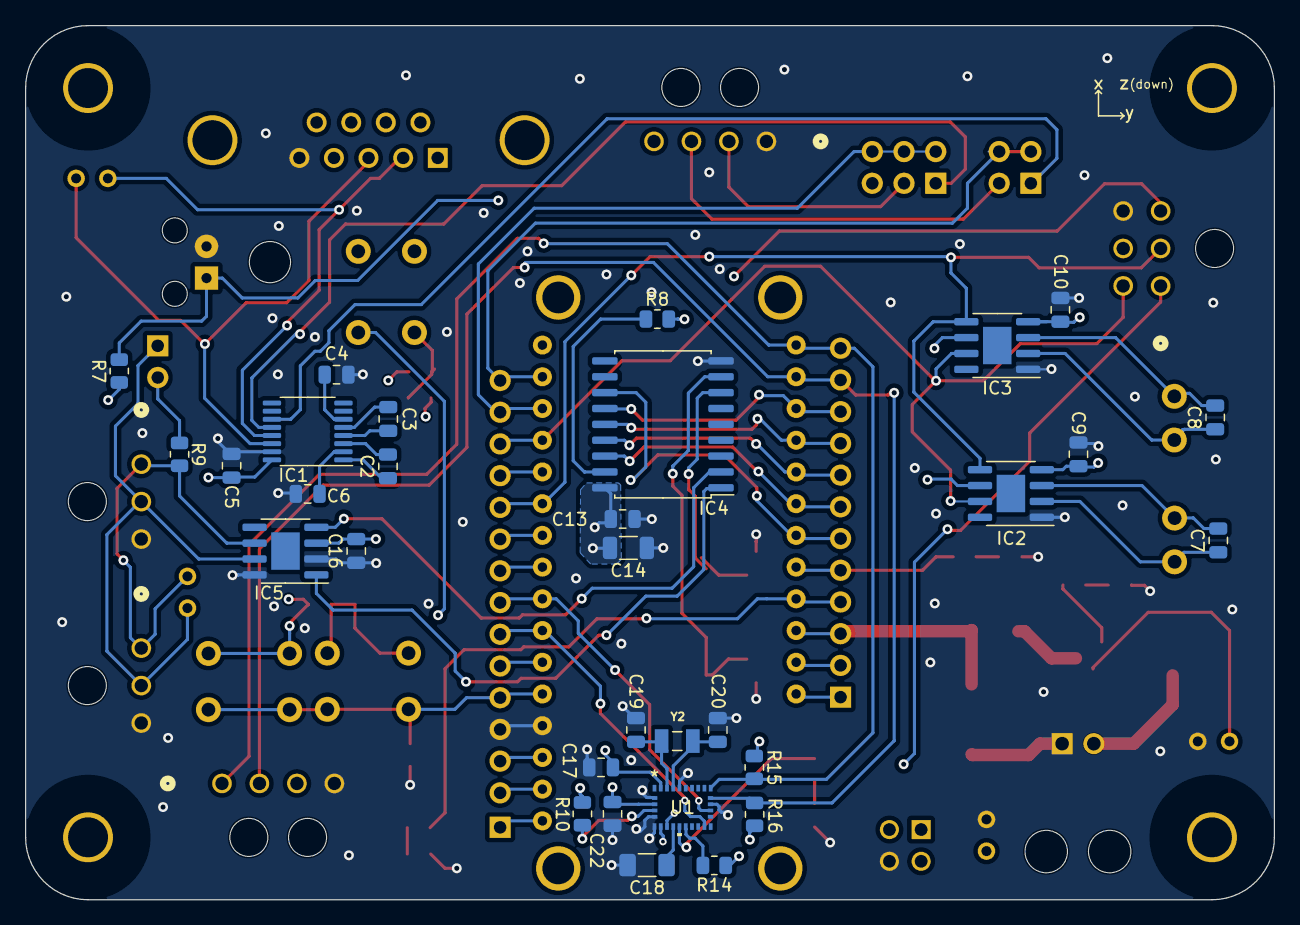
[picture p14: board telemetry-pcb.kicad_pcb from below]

Board: 4 copper layers, 100.0 x 70.0 mm, 78 parts (31 on the bottom side), 69 nets.

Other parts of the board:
CN4: GPS; CONN_SD-43650-001_04_MOL

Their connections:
+3V3: CN4.3; also elsewhere on the board
/SCL: CN4.2; also elsewhere on the board
/SDA: CN4.1; also elsewhere on the board
GND: CN4.4; also elsewhere on the board

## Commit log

2021-01-22 finished first draft of Electron schematic
    [telemetry-pcb.kicad_pcb, telemetry-pcb.sch]
2021-01-23 replaced headers with screw terminals, placed 12v off board
    [telemetry-pcb.sch]
2021-01-27 finished schematic with 12v off-board input and outputs as specified on Notion
    [telemetry-pcb.sch]
2021-01-27 added fan connector
    [telemetry-pcb.sch]
2021-01-27 added first draft of BOM
    [BOM.xlsx, telemetry-pcb.sch]
2021-01-27 fixed design rule violations and added input diode
    [BOM.xlsx, telemetry-pcb.sch]
2021-01-27 removed trailing wire under R1
    [telemetry-pcb.sch]
2021-01-30 finalized schematic based on review feedback
    [telemetry-pcb.sch]
2021-02-01 laid out all components and got most footprints imported
    [BOM.xlsx, telemetry-pcb.kicad_pcb]
2021-02-03 finished first draft of PCB
    [BOM.xlsx, telemetry-pcb.kicad_pcb, telemetry-pcb.sch]
2021-02-03 cleaned up repo
    [telemetry-pcb.kicad_pcb, telemetry-pcb.sch]
2021-02-05 added references to silkscreen and fixed Molex SL footprint soldermask
    [telemetry-pcb.kicad_pcb, telemetry-pcb.sch]
2021-02-06 fixed molex sl 2pos footprint
    [telemetry-pcb.kicad_pcb]
2021-02-15 finished first draft of schematic with Boron
    [BOM.xlsx, telemetry-pcb.sch]
2021-02-15 finished first draft of schematic for Boron
    [BOM.xlsx, telemetry-pcb.sch]
2021-02-15 finished footprint selection, placement, and silkscreen.
    [BOM.xlsx, telemetry-pcb.kicad_pcb, telemetry-pcb.sch]
2021-02-27 finished PCB routing
    [telemetry-pcb.kicad_pcb]
2021-03-10 updated PCB to fix two errors: TX/RX were switched on DB9 jack, and SPI was not connected to MAX31855 ICs
    [BOM.xlsx, telemetry-pcb.kicad_pcb, telemetry-pcb.sch]
2021-03-20 made some final changes to PCB and BOM
    [BOM.xlsx, telemetry-pcb.kicad_pcb, telemetry-pcb.sch]
2021-05-08 Adding PCBway fab files
    [telemetry-pcb-B_Cu.gbl, telemetry-pcb-B_Mask.gbs, telemetry-pcb-B_Paste.gbp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]
2021-09-08 revert before everything was messed up
    [BOM.xlsx, telemetry-pcb.kicad_pcb, telemetry-pcb.sch]
2021-09-08 fixed merge issues
    [telemetry-pcb.kicad_pcb]
2021-09-09 small changes and gerber file for JLPCB
    [telemetry-pcb-B_Cu.gbl, telemetry-pcb-B_Mask.gbs, telemetry-pcb-B_SilkS.gbo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]
2021-09-10 added JLPCB gerber files
    [BOM.xlsx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]
2021-09-17 updated BOM with some missing items + external connectors
    [BOM.xlsx]
2021-11-02 started on 1.1 redesign, schematic is done and PCB has just been started.
    [mcu_i2c.sch, power_can.sch, serial.sch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]
2022-02-25 finished schematic and PCB layout for 1.1 board
    [serial.sch, spi.sch, telemetry-pcb.kicad_pcb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]
2022-02-25 routed all
    [telemetry-pcb.kicad_pcb, telemetry-pcb.sch]
2022-03-03 removes one power port, changes CAN switch to jumper
    [serial.sch, spi.sch, telemetry-pcb.kicad_pcb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]
2022-03-03 updates PCB to move serial headers next to serial ports, CAN header next to CAN ports
    [telemetry-pcb.kicad_pcb]
2022-03-04 Updates BOM
    [BOM.xlsx, spi.sch, telemetry-pcb.kicad_pcb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]
2022-03-04 added bottom silkscreen logo, date, and names
    [telemetry-pcb.kicad_pcb]
2022-03-04 deleted extraneous footprints
    [mcu_i2c.sch, power_can.sch, serial.sch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]
2022-03-08 Shrinks board and removes GPS. Replaces GPS with Qwiic connector for off-board GPS
    [BOM.xlsx, telemetry-pcb.kicad_pcb, telemetry-pcb.sch]
2022-03-14 changes CAN ports to 3 pin, Thermocouple ports to 2 pin
    [BOM.xlsx, spi.sch, telemetry-pcb.kicad_pcb]
2022-07-29 minor changes to serial port - update rs232 connector and delete GND connection
    [serial.sch, telemetry-pcb.kicad_pcb]
2022-08-02 fixes optical receiver wiring and changes GPS connector to JST GH
    [serial.sch, telemetry-pcb.kicad_pcb, telemetry-pcb.sch]
2022-08-04 some more small changes from design review
    [serial.sch, spi.sch, telemetry-pcb.kicad_pcb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]
2022-08-09 2-0 complete
    [BOM.xlsx, telemetry-pcb.kicad_pcb]
2022-08-10 adds gerber files
    [telemetry-pcb-B_Cu.gbl, telemetry-pcb-B_Mask.gbs, telemetry-pcb-B_Paste.gbp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]
2022-11-19 fixes button issue
    [serial.kicad_sch, spi.kicad_sch, telemetry-pcb.kicad_pcb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]
2022-11-19 fixed power flag in schematic causing error
    [serial.kicad_sch, spi.kicad_sch, telemetry-pcb.kicad_pcb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]
2022-11-20 creates gerber files
    [telemetry-pcb-B_Cu.gbl, telemetry-pcb-B_Mask.gbs, telemetry-pcb-B_Paste.gbp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]
2022-11-20 updates gerber files to kicad standards, changes version number and date on silkscreen
    [telemetry-pcb-B_Cu.gbl, telemetry-pcb-B_Mask.gbs, telemetry-pcb-B_Paste.gbp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]
2025-10-25 3.0 Preliminary Changes
    [serial.kicad_sch, spi.kicad_sch, telemetry-pcb.kicad_pcb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]
2025-12-02 Completed PCB routing
    new footprints added to Footprints folder, added I2C peripherals page.
    [039301040.stp, i2c.kicad_sch, serial.kicad_sch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]
2025-12-09 added logo
    [telemetry-pcb.kicad_pcb]
2025-12-09 review me
    [telemetry-pcb.kicad_pcb]

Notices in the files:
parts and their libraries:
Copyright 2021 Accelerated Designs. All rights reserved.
